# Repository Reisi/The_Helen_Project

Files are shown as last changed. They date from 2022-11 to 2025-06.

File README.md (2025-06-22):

# Helen

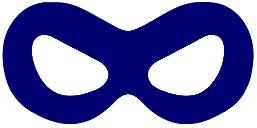
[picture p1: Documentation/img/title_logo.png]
Helen


The Helen Project is a firmware platform for bicycle lights.
It features

- up to 8 modes, each individually configurable
- the modes can be split into groups
- support for remote control connected over BLE
- mode and group configurations with The Helen App
- light-to-light connections with mode synchronization

Currently there are two devices:

- [Helen](HELEN.md), an alternative electronic circuit for the Yinding or KD2 headlight cycling lamps
- [Drake](https://github.com/Reisi/Drake), a multi-purpose PCB, which can be used to build a rear light or a dropper post actuator

## License

This project is licensed under the BSD-2-clause License - see the [license.txt](license.txt) file for details

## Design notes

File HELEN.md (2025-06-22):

# Helen

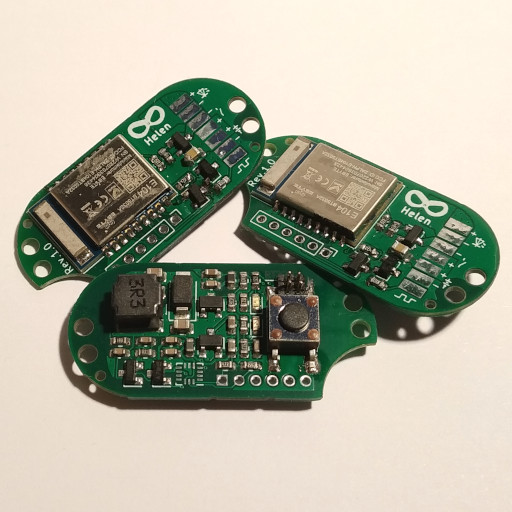
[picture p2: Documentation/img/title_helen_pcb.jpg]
Helen
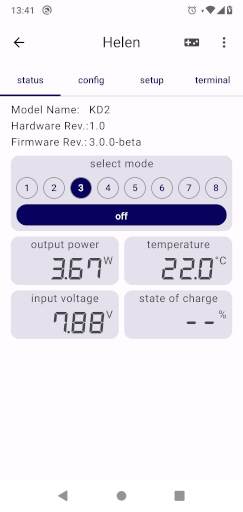
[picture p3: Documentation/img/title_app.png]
app
 

Helen is an alternative circuit board for the Yinding or KD2 headlight cycling lamps

## Main Features

- Step-Down current converter with up to 3A.
- Linear power reduction at low battery and high temperature.
- Standby current less than 100µA.
- Supports 1 (one LED), 2 (one or two LEDs) or 3 (up to three LEDs in series) cell Li-Ion battery.
- optionally: An integrated motion sensor to control the output current to reduce glare when looking down.
- optionally: A 3A PWM source.
- optionally: A multi-functional com pin, can be used for wired communication, an external button or a low power PWM source
- support for the Helena Base Driver to add two additional 3A current sources.

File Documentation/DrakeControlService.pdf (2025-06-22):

## Drake Control Service

## Base UUID: 4F770000ED7D-11E4-840E-0002A5D5C51B

## Service UUID: 0x0601

## Abstract:

This service exposes board specific control methods .

## Summary:

### TODO

## Service Dependencies:

This service is not dependent upon any other service.

## GATT Requirements

Sub-Procedure | Server Requirement
Write Characteristic Value | Mandatory
Notifications | Excluded
Indications | Mandatory
Read Characteristic Descriptors | Mandatory
Write Characteristic Descriptors | Mandatory

## Transport Dependencies

Transport | Supported
Classic | false
Low Energy | true
High Speed | false

## Error Codes

Name | Code | Description

## Service Characteristics

Overview | Properties | Security | Descriptors
Name: Drake Status Requirement: Optional | | | None
Property | Requirement | | Overview | Permissions
Perm. | Req.
Read | Mandatory
Write | Mandatory
Read | Mandatory
Write | Excluded
WriteWithoutResponse | Excluded
SignedWrite | Excluded
Notify | Mandatory
Indicate | Excluded
WriteableAuxiliaries | Excluded
Broadcast | Excluded
ExtendedProperties
Name: Drake Feature Requirement: Mandatory | | None | None

Name:
Client
Characteristic
Configuration
Requirement:
Mandatory
Property | Requirement
Read | Mandatory
Write | Excluded
WriteWithoutResponse | Excluded
SignedWrite | Excluded
Notify | Excluded
Indicate | Excluded
WriteableAuxiliaries | Excluded
Broadcast | Excluded
ExtendedProperties
Name: Drake Control Point Requirement: Mandatory | Property | Requirement | Optional | Overview | Permissions
Read | Excluded | | Name: Client Characteristic Configuration Requirement: Mandatory
Perm. | Req.
Write | Mandatory | | | Read | Mandatory
WriteWithoutResponse | Excluded | | | Write | Mandatory
SignedWrite | Excluded
Notify | Excluded
Indicate | Mandatory
WriteableAuxiliaries | Excluded
Broadcast | Excluded
ExtendedProperties

## Drake Status

## Characteristic UUID: 0x0602

## Summary:

The Drake Staus characteristic is a variable length structure containing a Flags field and, based on the contents of the Flags field, may contain one or more additional fields as shown in the table below.

## Value Fields

Names | Field Req. | Format | Additional Information
Flags | Mandatory | 8bit | Bit Field
Bit | Size | Name | Definition
0 | 1 | plunger status present
0 | False
1 | True
1 | 7 | reserved for future use
Plunger Status Information: Unit is in percent with a resolution of 0.5 Unit: org.bluetooth.unit.percentage Exponent: Binary, -1 | Optional | uint8 | 0% closed 100% fully opened

## Drake Feature

## Characteristic UUID: 0x0603

## Summary:

The Drake Feature characteristic is used to report a list of features supported by the device.

## Value Fields

Names | Field Req. | Format | Additional Information
Device Features | Mandatory | 8bit | Bit Field
Bit | Size | Name | Definition
0 | 1 | light supported
0 | False
1 | True
1 | 1 | seat-post actuator supported
0 | False
1 | True
2 | 6 | reserved for future use
Light Features | Mandatory | 8bit | Bit Field
Bit | Size | Name | Definition
0 | 1 | front-light pattern supported
0 | False
1 | True
1 | 1 | tail-light pattern supported
2 | 1 | position-light pattern supported | 0 | False
| | | 1 | True
3 | 1 | brake-light pattern supported
0 | False
1 | True
0 | False
1 | True
4 | 1 | left indicator-light pattern supported
0 | False
1 | True
5 | 1 | right indicator-light pattern supported
6 | 2 | reserved for future use
Actuator Features | Mandatory | 8bit | Bit Field
Bit | Size | Name | Definition
0 | 1 | motor configuration supported | 0 | False
| | | 1 | True
0 | False
1 | True

1 | 1 | motor sensor supported | 0 | False 1 True
2 | 1 | travel sensor supported
| | | 0 | False 1 True
4 | 4 | reserved for future use
0 | False 1 True
3 | 1 | travel indexing supported

## Drake Control Point

## Characteristic UUID: 0x0604

## Summary:

The Drake Control Point characteristic is used to request a specific function to be executed on the receiving device.

## Value Fields

Names | Field Req. | Format | Additional Information
Op codes | Mandatory | uint8 | Enumerations
Key | Value | Description
1 | request device usage | Request the devices main usage. The response to this control point is 0x20 followed by the devices usage. See Table 1: Device usage enumeration for usage definitions.
2 | set device usage | Initiate the procedure to set the devices main usage. The new usage is sent with preceding Op Code 0x02. The response to this control point is 0x20. See Table 1: Device usage enumeration for usage definitions.
3 | request battery information | Request the battery information. The response to this control point is 0x20 followed by the battery information See Table 2: Battery information for battery information definitions
4 | set battery information | Initiate the procedure to set the battery information. The new information is sent with preceding Op Code 0x04. The response to this control point is 0x20. See Table 2: Battery information for battery information definitions
5 | request soc at startup timeout | Request the state of charge at startup timeout. The response to this control point is 0x20 followed by the timeout in 1/1024s. This represents the length of one morse dot when device is used at dropper actuator and when device is used at light it represents the time in 1/1024s the indication is shown.

6 | set soc at startup timeout | Initiate the procedure to set the state of charge at startup timeout. The new timeout is sent with preceding Op Code 0x06. The response to this control point is 0x20. This represents the length of one morse dot when device is used at dropper actuator and when device is used at light it represents the time in 1/1024s the indication is shown.
7 | request light pattern | Request the current light pattern. The desired light type is sent as an uint8 with preceding Op Code 0x07. The response to this control point is 0x20 followed by the light type as uint8 and pattern as an array of uint8. See Table 3: Light type enumeration for light types and Table 4: Pattern description for pattern description.
8 | set light pattern | Initiate the procedure to change the light pattern. The desired light type (as uint8) and new pattern (as an array of uint8) is sent with preceding Op Code 0x08. The response to this control point is 0x20. See Table 3: Light type enumeration for light types and Table 4: Pattern description for pattern description.
10 | set plunger position | Initiate the procedure to set the plunger opening value. The requested opening value (in percent with a resolution of 0.5) is sent with preceding Op Code 0x09. The response to this control point is Op Code 0x20.
11 | request motor configuration | Request the current motor configuration. The response to this Op Code is 0x20 followed by the motor configuration. See Table 5: Motor configuration for configuration description.
12 | set motor configuration | Initiate the procedure to set the motor configuration. The new configuration is sent with preceding Op Code 0x0C. The response to this control point is 0x20. See Table 5: Motor configuration for configuration description.

13 | request motor sensor calibration | Request the motor sensor calibration data. The desired calibration type is sent with preceding Op Code 0x0D. The response to this control point is 0x20 followed by the calibration data. See Table 6: Motor sensor calibration data for sensor calibration data
14 | clear/start motor sensor calibration | Initiate the procedure to clear or start the desired motor sensor calibration. The desired calibration type is sent as uint8 with preceding Op Code 0x0E, followed by 0 to clear current data or 1 to start the calibration. The response to this control point is 0x20 followed by the new calibration data (in case of starting). See Table 6: Motor sensor calibration data for sensor calibration data
15 | request travel sensor data | Request the travel sensor data. The response to this control point is 0x20 followed by the sensor data data. See Table 7: Travel sensor data for sensor data
16 | clear/start motor sensor calibration | Initiate the procedure to clear or start the travel sensor calibration. To clear the sensor data send Op Code 0x10 without any data. To start the calibration send Op Code ßx10 followed with the seatpost travel in mm (as uint16). The response to this control point is 0x20 followed by the new sensor data (in case of starting). See Table 7: Travel sensor data for sensor data
17 | request indexed travel configuration | Request the indexed travel configuration. The response to this control point is 0x20 followed by the configuration. See Table 8: Indexed travel configuration
18 | set indexed travel configuration | Initiate the procedure to set the indexed travel configuration. The new configuration is sent with preceding Op Code 0x12. The response to this control point is 0x20. See Table 8: Indexed travel configuration
32 | Response Code | The response code is followed by the requested Op Code, the response value and optionally the response parameter

0-0 | Reserved for future use
15-31 | Reserved for future use
33-255 | Reserved for future use
Parameter Value | Optional | variable | Refer to the Op Code table above for additional information on the possible values for this filed
Request Op Code Information: The Request Op Code is a sub field of the Parameter Value for "Response Code" Op Code. C1: This Field is Mandatory for "Response Code" Op Code, otherwise this field is Excluded. | C1 | uint8 | Refer to the Op Code table above for additional information on the possible values for this filed
Response Value Information: The Request Op Code is a sub field of the Parameter Value for "Response Code" Op Code. C1: This Field is Mandatory for "Response Code" Op Code, otherwise this field is Excluded. | C1 | uint8 | Enumerations
Key | Value | Description
1 | Success | Response for successful operation.
2 | Op Code not supported | Response if unsupported Op Code is received.
3 | Invalid Parameter | Response if Parameter received does not meet the requirements of the service or is outside of the supported range
4 | Operation Failed | Response if the requested procedure failed
0-0 | Reserved for future use
5-255 | Reserved for future use
Response Parameter Information: The Response Parameter is a sub field of the Parameter Value for "Response Code" Op Code. C2:This Field is Optional for "Response Code" Op Code, otherwise this field is Excluded. | C2 | variable | Note: The Response Parameter Value of the response to the Control Point is a variable length field to allow a list of different values defined by the Service Specification
Key | Name | Additional Information
0 | Dropper actuator
16 | 16 LED rear light
44 | 44 LED rear light
1-15, 17-43, 45-255 | Reserved for future use

### Table 1: Device usage enumeration

Name | Format | Additional Information
type | | | cell chemistry
Key | Name
0 | LCO
1 | NMC
1-255 | Reserved for future use
design capacity Information: Unit is in Coulomb with a resolution of 1 Unit: org.bluetooth.unit.elctric_charge_coulomb Exponent: Decimal, 0 | uint16
actual capacity Information: Unit is in Coulomb with a resolution of 1 Unit: org.bluetooth.unit.elctric_charge_coulomb Exponent: Decimal, 0 | uint16 | This information is only mandatory when requesting. When setting the battery information this filed is excluded.

### Table 2: Battery information

Key | Name | Additional Information
0 | Front light
1 | Rear light
2 | Position light
3 | Brake indicator light
4 | Left indicator light
5 | Right indicator light
6-255 | Reserved for future use

### Table 3: Light type enumeration

Name | Format | Additional Information
pattern | array of uint8
| bit 7 | bit 6 | bit 5 | bit 4 | bit 3 | bit 2 | bit 1 | bit 0
pattern[0] | LED8 | LED7 | LED6 | LED5 | LED4 | LED3 | LED2 | LED1
pattern[1] | LED16 | LED15 | LED14 | LED13 | LED12 | LED11 | LED10 | LED9
pattern[n] | LED8n | LED8n-1 | LED8n-2 | LED8n-3 | LED8n-4 | LED8n-5 | LED8n-6 | LED8n-7

### Table 4: Pattern description

Name | Format | Additional Information
open timeout Information: Unit is in seconds with a resolution of 1/1024 Unit: org.bluetooth.unit.time.second Exponent: Binary, -10 | uint16 | The time the actuator motor will be activated to open. This timeout is only used if no motor sensor is available or not calibrated yet
close timeout Information: Unit is in seconds with a resolution of 1/1024 Unit: org.bluetooth.unit.time.second Exponent: Binary, -10 | uint16 | The time the actuator motor will be activated to close

### Table 5: Motor configuration

Name | Format | Additional Information

calibration type

Key | Name
0 | comp threshold | the comparator thresholds used for the sensor
1 | full open count | the number of counts until the plunger is in fully open position
2-255 | Reserved for future use
upper comp threshold Information: Unit-less with a resolution of 1 Exponent: Decimal, 0 Information: This field is mandatory for “comp threshold”, otherwise excluded | uint8 | If both, upper and lower thresholds are 0, sensor hasn’t been calibrated yet
lower comp threshold Information: Unit-less with a resolution of 1 Exponent: Decimal, 0 Information: This field is mandatory for “comp threshold”, otherwise excluded | uint8
full open count Information: Unit-less with a resolution of 1 Exponent: Decimal, 0 Information: This field is mandatory for “fully open count”, otherwise excluded | uint16

### Table 6: Motor sensor calibration data

Name | Format | Additional Information
seatpost travel Information: Unit is in millimeters with a resolution of 1 Unit: org.bluetooth.unit.length.metre Exponent: Decimal, -3 | uint16
sensor offset Information: Unit is in micrometers with a resolution of 1 Unit: org.bluetooth.unit.length.metre Exponent: Decimal, -6 | int32

### Table 7: Travel sensor data

Name | Format | Additional Information
opening blocking time Information: Unit is in seconds with a resolution of 1/1024 Unit: org.bluetooth.unit.time.second Exponent: Binary, -10 | uint16 | The time the opening position is ignored
closing timeout Information: Unit is in seconds with a resolution of 1/1024 Unit: org.bluetooth.unit.time.second Exponent: Binary, -10 | uint16 | The timeout to close when no indexed position is reached.
indexed positions Information: Unit is in millimeters with a resolution of 1 Unit: org.bluetooth.unit.length.metre Exponent: Decimal, -3 | array of int16

### Table 8: Indexed travel configuration

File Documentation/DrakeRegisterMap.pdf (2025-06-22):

## Drake I2C Register Map

Name | Address | bit 7 | bit 6 | bit 5 | bit 4 | bit 3 | bit 2 | bit 1 | bit 0
PWR | 0x00 | | | | | | | | SYS OFF
STATUS0 | 0x01 | | | | | | | TPR | MPR
STATUS1 | 0x02 | | | TOR | MOR | | | TDR | MDR
MDATA | 0x03 | MT_POS
TDATA | 0x04 | TRV_DATA
WHOAMI | 0x05 | WHO_AMI
MTCFG0 | 0x06 | DC_OPEN
MTCFG1 | 0x07 | DC_CLOSE
MTCFG2 | 0x08 | TIMEOUT_OPEN
MTCFG3 | 0x09 | TIMEOUT_CLOSE
MTCAL0 | 0x0A | | | FOS | THS | | | FOC | THC
MTCAL1 | 0x0B | | | | THR_LOW
MTCAL2 | 0x0C | | | | THR_UP
MTCAL3 | 0x0D | FULL_OPEN_L
MTCAL4 | 0x0E | FULL_OPEN_H
TRVCAL0 | 0x0F | | | | | | | | TOC
TRVCAL1 | 0x10 | TRV_POST_L
TRVCAL2 | 0x11 | TRV_POST_H
TRVCAL3 | 0x12 | TRV_OFF_L
TRVCAL4 | 0x13 | TRV_OFF_H
INDCFG0 | 0x14 | OPEN_BLOCKING
INDCFG1 | 0x15 | CLOSE_TIMEOUT
INDPOS0 | 0x16 | INDEX_POS0
INDPOS1 | 0x17 | INDEX_POS1
INDPOS2 | 0x18 | INDEX_POS2
INDPOS3 | 0x19 | INDEX_POS3

## Drake I2C Register Description

## PWR (0x00)

0 | 0 | 0 | 0 | 0 | 0 | 0 | SYS_OFF
SYS_OFF | | System off read/write default value: 0

0: system on; 1 system off
write 1 to request system off mode, device will automatically wake up on
| | bus activity

## STATUS0 (0x01)

0 | 0 | 0 | 0 | 0 | 0 | TPR | MPR
MPR | Motor position sensor present read only 0: sensor not present; 1: sensor present if sensor not present write operation to corresponding registers (MTCFG, MTCAL) have no effect
TDR | Travel sensor present read only 0: sensor not present; 1: sensor present if sensor not present write operation to corresponding registers (TRVCFG, TRVCAL) have no effect

## STATUS1 (0x02)

0 | 0 | TOR | MOR | 0 | 0 | TDR | MDR
MDR | Motor position data ready read only default value: 0 0: no new data; 1: new data available will be cleared by reading MDATA register
TDR | Travel data ready read only default value: 0 0: no new data; 1: new data available will be cleared by reading TDATA registers
MOR | Motor position data overrun read only 0: no overrun occurred; 1: previous data has been overwritten will be cleared by reading MDATA register
TOR | Travel data overrun read only 0: no overrun occurred; 1: previous data has been overwriten will be cleared by reading TDATA registers

## MDATA (0x03)

Motor position sensor data
read only
represents the motor position in q8_t (255..0 → 100..0%)

## TDATA (0x04)

Travel sensor data
read only
represents the travel in q8_t (255..0 → 100..0%)

## WHOAMI (0x05)

Who Am I
read onla
default value: 0xDE

## MTCFG0 (0x06)

Motor configuration register 0, duty cycle open read/write
represents the duty cycle used when motor is opening

## MTCFG1 (0x07)

Motor configuration register 1, duty cycle close read/write
represents the duty cycle used when motor is closing

## MTCFG2 (0x08)

Motor configuration register 2, timeout open
read/write
represents the motor timeout in 1/128s used when motor is opening

## MTCFG3 (0x09)

Motor configuration register 3, timeout close
read/write
represents the motor timeout in 1/128s used when motor is closing

## MTCAL0 (0x0A)

0 | 0 | FOS | THS | 0 | 0 | FOC | THC
THC | Threshold calibration data clear write only 0: no change; 1: threshold calibration data will be cleared
FOC | Full open calibration data clear write only 0: no change; 1: full open calibration data will be cleared
THS | Threshold calibration start write only 0: no change; 1: start threshold calibration
FOS | Full open calibration start write only 0: no change; 1: start full open calibration

## MTCAL1 (0x0B)

0 | 0 | 0 | | | THR_LOW
THR_LOW | Lower threshold calibration data
| | read only

## MTCAL2 (0x0C)

0 | 0 | 0 | | | THR_UP
THR_UP | Upper threshold calibration data
| | read only

## MTCAL3 (0x0D), MTCAL4 (0x0E)

Motor calibration register 3 and 4, full open calibration data read only

## TRVCAL0 (0x0F)

0 | 0 | 0 | 0 | 0 | 0 | 0 | TOC
T=C | Travel Offset calibration data clear
| | write only
0: no change; 1: offset calibration data will be cleared

## TRVCAL1 (0x10), TRVCAL2 (0x11)

Travel calibration register 1 and 2, seatpost travel read/write (write initiates offset calibration) represents the total travel of the seatpost in mm

## TRVCAL3 (0x12), TRVCAL4 (0x13)

Travel calibration register 3 and 4, travel sensor offset read only
represents the offset in µm (might be changed in future)

## INDCFG0 (0x14)

Indexed travel configuration register 0, opening blocking time read/write
represents the opening blocking time in 1/64s

## INDCFG1 (0x15)

Indexed travel configuration register 1, closing timeout read/write
represents the closing timeout in 1/64s

## INDPOS0 (0x16) - INDPOS3 (0x19)

Indexed travel position registers 0 to 3, indexed positions 0 - 3 read/write
represents indexed positions in q8_t

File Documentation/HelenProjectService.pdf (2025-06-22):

## Helen Project Service

## Base UUID: 4F770000ED7D-11E4-840E-0002A5D5C51B

## Service UUID: 0x0301

## Abstract:

### This service exposes measurement and control methods

## Summary:

### TODO

## Service Dependencies:

This service is not dependent upon any other service.

## GATT Requirements

Sub-Procedure | Server Requirement
Write Characteristic Value | Mandatory
Notifications | C1
Indications | Mandatory
Read Characteristic Descriptors | Mandatory
Write Characteristic Descriptors | Mandatory
C1: Mandatory if the Helen Measurement characteristic is supported, otherwise excluded for this service.

## Transport Dependencies

Transport | Supported
Classic | false
Low Energy | true
High Speed | false

## Error Codes

Name | Code | Description

## Service Characteristics

Overview | Properties | Security | Descriptors
Name: Helen Measurement Requirement: Optional | | | None
Property | Requirement | | Overview | Permissions
Perm. | Req.
Read | Mandatory
Write | Mandatory
Read | Excluded
Write | Excluded
WriteWithoutResponse | Excluded
SignedWrite | Excluded
Notify | Mandatory
Indicate | Excluded
WriteableAuxiliaries | Excluded
Broadcast | Excluded
ExtendedProperties
Name: Helen Feature Requirement: Mandatory | | None | None

Name:
Client
Characteristic
Configuration
Requirement:
Mandatory
Property | Requirement
Read | Mandatory
Write | Excluded
WriteWithoutResponse | Excluded
SignedWrite | Excluded
Notify | Excluded
Indicate | Excluded
WriteableAuxiliaries | Excluded
Broadcast | Excluded
ExtendedProperties
Name: Helen Modes Requirement: Mandatory | Property | Requirement | Optional for write property | None
| Read | Mandatory
| Write | Optional
| WriteWithoutResponse | Excluded
| SignedWrite | Excluded
| Notify | Excluded
| Indicate | Excluded
| WriteableAuxiliaries | Excluded
| Broadcast | Excluded
| ExtendedProperties

Name: Helen Control Point Requirement: Mandatory | Optional
Property | Requirement | Overview | Permissions
Read | Excluded | Name: Client Characteristic Configuration Requirement: Mandatory | Perm. | Req.
Write | Mandatory
| | | Read | Mandatory
WriteWithoutResponse | Excluded
| | | Write | Mandatory
SignedWrite | Excluded
Notify | Excluded
Indicate | Mandatory
WriteableAuxiliaries | Excluded
Broadcast | Excluded
ExtendedProperties
Name: Helen Support Requirement: Mandatory | | Optional
Property | Requirement | Overview | Permissions
Perm. | Req.
Read | Mandatory
Read | Excluded
Write | Excluded
WriteWithoutResponse | Excluded
SignedWrite | Excluded
Notify | Mandatory
Indicate | Excluded
WriteableAuxiliaries | Excluded
Broadcast | Excluded
ExtendedProperties

Name:
Client
Characteristic
Configuration
Requirement:
Mandatory

Write Mandatory

## Helen Measurement

## Characteristic UUID: 0x0302

## Summary:

The Helen Measurement characteristic is a variable length structure containing a Flags field and, based on the contents of the Flags field, may contain one or more additional fields as shown in the table below.

## Value Fields

Names | Field Req. | Format | Additional Information
tbd. | Mandatory | 8bit | set to 0 until defined
Flags | Mandatory | 8bit | Bit Field
Bit | Size | Name | Definition
0 | 1 | output power present
0 | False
1 | True
1 | 1 | temperature present
2 | 1 | input voltage present | 0 | False
| | | 1 | True
3 | 1 | SOC present
0 | False
1 | True
0 | False
1 | True
4 | 4 | reserved for future use
Mode | Mandatory | 8bit | OFF: 255; SOS: 254; ON: 0..n-1
Output Power Information: Unit is in watts with a resolution of 1/1000. Unit: org.bluetooth.unit.power.watt Exponent: Decimal, -3 | Optional | uint16
Temperature Information: Unit is in degree Cesius with a resolution of 1.. Unit: org.bluetooth.unit.thermodynamic_t emperature.degree_celcius Exponent: Decimal, 0 | Optional | int8

Input Voltage Information: Unit is in volts with a resolution of 1/1000. Unit: org.bluetooth.unit.electric_potential _difference.volt Exponent: Decimal, -3 | Optional | uint16
State of charge Information: Unit is in percent with a resolution of 0.5 Unit: org.bluetooth.unit.percentage Exponent: Binary, -1 | Optional | uint8

## Helen Feature

## Characteristic UUID: 0x0303

## Summary:

The Helen Feature characteristic is used to report a list of features supported by the device.

## Value Fields

Names | Field Req. | Format | Additional Information
Mode Count | Mandatory | 8bit | the number of available modes
Channel Count | Mandatory | 8bit | the number of available channels
Channel Size | Mandatory if Channel Count > 0, otherwise excluded | 16bit | this field is present as array, one for each channel Bit Field
Bit | Size | Name | Definition
0 | 8 | channel bitsize | the total size in bits of the Channels Configuration Field for this channel
8 | 4 | special feature bitsize | the number of bits used for special feature
12 | 4 | channel description
Key | Name | Additional Information
0 | User | user specific channel
1 | Current | current regulated channel
2 | Voltage | voltage regulated channel
3 | PWM | PWM channel
4 | Switch | on/off channel
5-15 | reserved for future use
Features | Mandatory | 16bit | Bit Field
Bit | Size | Name | Definition
0 | 1 | mode set supported
0 | False
1 | True
1 | 1 | search request supported
0 | False
1 | True
2 | 1 | factory reset supported
3 | 1 | mode override supported | 0 | False
| | | 1 | True
4 | 12 | reserved for future use
0 | False
1 | True

## Helen Modes

## Characteristic UUID: 0x0304

## Summary:

The Helen Modes characteristic is used to modify the modes of the device.

## Value Fields

Names | Field Req. | Format | Additional Information
| | | Bit Field
Bit | Size | Name | Definition
0 | 1 | ignore
0 | False
1 | True
1 | 1 | First_In_Group
Mode Configuration | Mandatory | 16bit | This field is present as array, one field for each mode
0 | False
1 | True
2 | 1 | Last_In_Group
0 | False
1 | True
3 | 1 | Is_Preferred_Mo de
0 | False
1 | True
4 | 1 | Is_Temporary_M ode
5 | 1 | Is_Off_Mode | 0 | False
| | | 1 | True
6 | 10 | reserved for future use
0 | False
1 | True

Channels Configuration | Optional | Variable | This field is present as two-dimensional array, one for
| | | each channel and mode. [channel 0][mode 0] [channel 0][mode 1] [channel 0][mode 2] … [channel 1][mode 0] [channel 1][mode 1] [channel 1][mode 2] … [channel 2][mode 0] [channel 2][mode 1] [channel 2][mode 2] | Bit Field
Bit | Size | Name
0 | channel bitsize – special feature bitsize | intensity
channel bitsize – special feature bitsize | special feature bitsize | modus

## Helen Control Point

## Characteristic UUID: 0x0305

## Summary:

The Helen Control Point characteristic is used to request a specific function to be executed on the receiving device.

## Value Fields

Names | Field Req. | Format | Additional Information
Op codes | Mandatory | uint8 | Enumerations
Key | Value | Description
1 | request mode | Request the current mode. The response to this control point is Op Code 0x20 followed by the current mode
2 | set mode | Set mode command. The response to this control point is Op Code 0x20
3 | request search | Initiate the procedure to start the search for a remote or other compatible light. The response to this control point is Op Code 0x20.
5 | factory reset | Initiate the procedure to perform a factory reset The response to this control point is Op Code 0x20. If the current connection is bonded, the device will disconnect.
8 | override mode | Temporary override the channel configuration for the current mode with the given one.
32 | Response Code | The response code is followed by the requested Op Code, the response value and optionally the response parameter
0, 4, 7, 9-31, 33-255 | Reserved for future use
mode | Mandatory for “set mode” Op code, otherwise excluded | uint8_t
channel configuration | Mandatory for “override mode” Op code, otherwise excluded | Variable | A list of channel configurations for each channel

Request Op Code | Mandatory for "Response Code" Op Code, otherwise this field is Excluded. | uint8 | Refer to the Op Code table above for additional information on the possible values for this filed
Response Value | Mandatory for "Response Code" Op Code, otherwise this field is Excluded. | uint8 | Enumerations
Key | Value | Description
1 | Success | Response for successful operation.
2 | Op Code not supported | Response if unsupported Op Code is received.
3 | Invalid Parameter | Response if Parameter received does not meet the requirements of the service or is outside of the supported range
4 | Operation Failed | Response if the requested procedure failed
0-0 | Reserved for future use
5-255 | Reserved for future use
mode | Mandatory for "Response Code" Op Code with “request mode” Request Op Code, otherwise this field is Excluded. | uint8_t

## Helen Support

## Characteristic UUID: 0x0306

## Summary:

The Helen Support characteristic is a variable length structure containing a Flags field and, based on the contents of the Flags field, may contain one or more additional fields as shown in the table below.

## Value Fields

Names | Field Req. | Format | Additional Information
Flags | Mandatory | 16bit | Bit Field
Bit | Size | Name | Definition
0 | 1 | time reference present
0 | False
1 | True
1 | 1 | brake indication timestamp present | 0 | False
| | | 1 | True
2 | 1 | left indicator timestamp present
0 | False
1 | True
3 | 1 | right indicator timestamp present
0 | False
1 | True
4 | 1 | inclination present
0 | False
1 | True
5 | 11 | reserved for future use
Time reference Information: Unit is in seconds with a resolution of 1/1024. Unit: org.bluetooth.unit.time.second Exponent: Binary, -10 | Mandatory if brake indication, left indicator or right indicator timestamp is present, otherwise optional for central, excluded for peripherals | uint16 | This represents the local timestamp at the server side. A Central shall send their reference to connected peripherals. A connected peripheral shall synchronize their local timestamp to the received timestamp. When sending a brake, left or right indicator stop timestamp, the server shall also include their timestamp so that the client is able to determine the duration of the indication.
Brake Indication Stop timestamp Information: Unit is in seconds with a resolution of 1/1024. Unit: org.bluetooth.unit.time.second Exponent: Binary, -10 | Optional | uint16 | tbd.

Left Indicator Stop Timestamp Information: Unit is in seconds with a resolution of 1/1024. Unit: org.bluetooth.unit.time.second Exponent: Binary, -10 | Optional | uint16 | tbd.
Right Indicator Stop Timestamp Information: Unit is in seconds with a resolution of 1/1024. Unit: org.bluetooth.unit.time.second Exponent: Binary, -10 | Optional | uint16 | tbd.
Inclination Information: Unit is in degree with a resolution of 1/100. Unit: org.bluetooth.unit.plane_angle.degr ee Exponent: Decimal, -2 | Optional | int16 | tbd.

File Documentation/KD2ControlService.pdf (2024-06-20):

## KD2 Control Service

## Base UUID: 4F770000ED7D-11E4-840E-0002A5D5C51B

## Service UUID: 0x0501

## Abstract:

This service exposes board specific control methods .

## Summary:

### TODO

## Service Dependencies:

This service is not dependent upon any other service.

## GATT Requirements

Sub-Procedure | Server Requirement
Write Characteristic Value | Mandatory
Notifications | Excluded
Indications | Mandatory
Read Characteristic Descriptors | Mandatory
Write Characteristic Descriptors | Mandatory

## Transport Dependencies

Transport | Supported
Classic | false
Low Energy | true
High Speed | false

## Error Codes

Name | Code | Description

## Service Characteristics

Overview | Properties | Security | Descriptors
Name: KD2 Feature Requirement: Mandatory | | | None | None
Property | Requirement
Read | Mandatory
Write | Excluded
WriteWithoutResponse | Excluded
SignedWrite | Excluded
Notify | Excluded
Indicate | Excluded
WriteableAuxiliaries | Excluded
Broadcast | Excluded
ExtendedProperties
Name: KD2 Control Point Requirement: Mandatory | | | Optional
Property | Requirement | Overview | Permissions
Read | Excluded | Name: Client Characteristic Configuration Requirement: Mandatory
Perm. | Req.
Write | Mandatory
| | | Read | Mandatory
WriteWithoutResponse | Excluded
| | | Write | Mandatory
SignedWrite | Excluded
Notify | Excluded
Indicate | Mandatory
WriteableAuxiliaries | Excluded
Broadcast | Excluded
ExtendedProperties

## KD2 Feature

## Characteristic UUID: 0x0502

## Summary:

The KD2 Feature characteristic is used to report a list of features supported by the device.

## Value Fields

Names | Field Req. | Format | Additional Information
Configuration Features | Mandatory | 8bit | Bit Field
Bit | Size | Name | Definition
0 | 1 | channel configuration supported
0 | False
1 | True
1 | 1 | com pin mode supported
0 | False
1 | True
2 | 1 | internal compensation supported
0 | False
1 | True
3 | 1 | external (Helena driver board) compensation Supported
4 | 1 | imu calibration Supported
0 | False
1 | True
0 | False
1 | True
5 | 3 | reserved for future use
Channel Features | Mandatory | 8bit | Bit Field
Bit | Size | Name | Definition
0 | 1 | adaptive channel supported
0 | False
1 | True
1 | 7 | reserved for future use

## KD2 Control Point

## Characteristic UUID: 0x0503

## Summary:

The KD2 Control Point characteristic is used to request a specific function to be executed on the receiving device.

## Value Fields

Names | Field Req. | Format | Additional Information
Op codes | Mandatory | uint8 | Enumerations
Key | Value | Description
1 | request channel configuration | Request a channel configuration. The desired channel is sent as an uint8 with preceding Op Code 0x01. The response is Op Code 0x20 followed by the channel configuration. See Table 1: channel configuration for configuration definition
2 | set channel configuration s | Initiate the procedure to configure a channel. The new channel configuration is with preceding Op Code 0x02 operand and desired channel number. The response to this control point is Op Code 0x20. See Table 1: channel configuration for configuration definition
3 | request Com pin configuration | Request the current Com pin configuration setup. The response is Op Code 0x20 followed by the current configuration. See Table 2: com pin enumeration for com pin definitions.
4 | set Com pin configuration | Initiate the procedure to change the Com pin configuration. The new configuration is sent with preceding Op Code 0x08. The response to this control point is Op Code 0x20. See Table 2: com pin enumeration for com pin definitions.

5 | request internal compensatio n | Request the internal compensation values. The response is Op Code 0x20 followed by compensation values. See Table 3: internal compensation for internal compensation value definitions.
6 | set internal compensatio n | Initiate the procedure to set the internal compensation values. The new compensation values are sent with preceding Op Code 0x0A. The response to this control point is 0x20. See Table 3: internal compensation for internal compensation value definitions.
7 | request external (Helena driver board) compensatio n | Request the compensation values of connected Helena driver board. The desired driver board is sent as an uint8 with preceding Op Code 0x07. If no board number is given, the first driver is selected. The response is Op Code 0x20 followed by compensation values. See Table 4: Helena driver board compensation for external compensation value definitions.
8 | set external (Helena driver board) compensatio n values | Initiate the procedure to set the external compensation values. The new compensation values are sent with preceding Op Code 0x08 and desired driver number, if no driver number is given, the first one is selected. The response to this control point is 0x20. See Table 4: Helena driver board compensation for external compensation value definitions
9 | request the imu calibration state | Request the imu calibration state. The response is Op Code 0x20 followed by the state (0 or 1)
10 | initiate the imu calibration | Initiate the procedure to calibrate the imu. The response is Op Code 0x20
32 | Response Code | The response code is followed by the requested Op Code, the response value and optionally the response parameter
0-0 | Reserved for future use
11-31 | Reserved for future use

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

Name | Format | Additional Information
Full Output Power Information: Unit is in watts with a resolution of 1/1000. Unit: org.bluetooth.unit.power.watt Exponent: Decimal, -3 | uint16 | valid range: 0 .. 40W
Output Limit Information: Unit is is in percentage with a resolution of 1, in relation to maximum output power. Unit: org.bluetooth.unit.percentage Exponent: Decimal, 0 | uint8 | valid range: 0..100%
Optic Type Information: Unit-less with a resolution of 1/128 Exponent: Binary, -7 | uint8 | enumeration:
Key | Name | Additional Information
0 | non-applicable | to use if channel is not equipped with an optic
1 | 15° optic
2 | 22° optic
3 | 30° optic
4-255 | Reserved for future use
Optic Offset Information: Unit is in degree with a resolution of 1/100. Unit: org.bluetooth.unit.plane_angle.degree Exponent: Decimal, -2 | int16 | valid range: -180..180°

### Table 1: channel configuration

Key | Name | Additional Information
0 | not used | com pin not used
1 | com | com pin used for communication
2 | button | com pin used as external button
3 | pwm | com pin used as active low open drain PWM signal
4-255 | Reserved for future use

### Table 2: com pin enumeration

Name | Format | Additional Information
voltage gain factor | uint16 | not used yet
voltage offset | int16 | not used yet
current gain factor Information: Unit-less with a resolution of 1/32768 Exponent: Binary, -15 | uint16
current offset | int16 | not used yet
temperature gain factor | uint16 | not used yet
temperature offset Information: Unit is in degree Celcius with a resolution of 1/128 Unit: org.bluetooth.unit.thermodynamic_t emperature.degree_celsius Exponent: Binary, -7 | int16

### Table 3: internal compensation

Name | Format | Additional Information
temperature offset Information: Unit is in degree Celcius with a resolution of 1/4 Unit: org.bluetooth.unit.thermodynamic_t emperature.degree_celsius Exponent: Binary, -2 | int16
left side current gain factor Information: Unit-less with a resolution of 1/128 Exponent: Binary, -7 | uint8
right side current gain factor Information: Unit-less with a resolution of 1/128 Exponent: Binary, -7 | uint8

### Table 4: Helena driver board compensation

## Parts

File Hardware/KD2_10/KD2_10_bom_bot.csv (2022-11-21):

Comment | Designator | Footprint | LCSC Part #
Conn_01x06 | J3
Conn_01x01 | J5 J7 J8 J1 J2 J4 J6
10 | R12 R13 | 0603 | C22859
5v6 | D5 | SOT-23-3 | C68542
2N7002 | Q2 | SOT-23-3 | C8545
4k7 | R11 | 0603 | C23162
10u/25V | C12 | 0805 | C15850
AO3400A | Q3 | SOT-23-3L | C20917
47k | R14 | 0603 | C25819
E104-BT5032A | U2 | WIRELM-SMD | C518912

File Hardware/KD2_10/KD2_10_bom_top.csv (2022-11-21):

Comment | Designator | Footprint | LCSC Part #
BMI160 | U1 | LGA-14 | C94021
SW_Push | SW1 | SMD-4_6.0x6.0x4.5P | C381064
SE8530X2-HF | U4 | SOT-23-3 | C115014
4µ7/16V | C9 C10 C2 | 0603 | C19666
100n | C4 C7 C11 C1 C8 C6 | 0603 | C14663
LED_RED | D4 | LED_0603 | C2286
LED_BLUE | D3 | LED_0603 | C72041
820 | R8 R6 | 0603 | C23253
120 | R7 | 0603 | C22787
Ferrite_Bead_Small | FB1 FB2 | 0603 | C1002
47k | R10 R5 | 0603 | C25819
1M | R9 | 0603 | C22935
4k7 | R3 R2 | 0603 | C23162
10 | R4 | 0603 | C22859
AO3400A | Q1 | SOT-23-3L | C20917
3µ-18 | L1 | IND-SMD | C83456
10u/25V | C3 C5 | 0805 | C15850
SS34 | D1 | SMA,DO-214AC | C8678
1k5 | R1 | 0603 | C22843
ZXCT1009F | U3 | SOT-23-3 | C83670
BAV99 | D2 | SOT-23-3 | C2500
dnp | J9

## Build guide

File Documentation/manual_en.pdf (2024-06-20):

# Helen

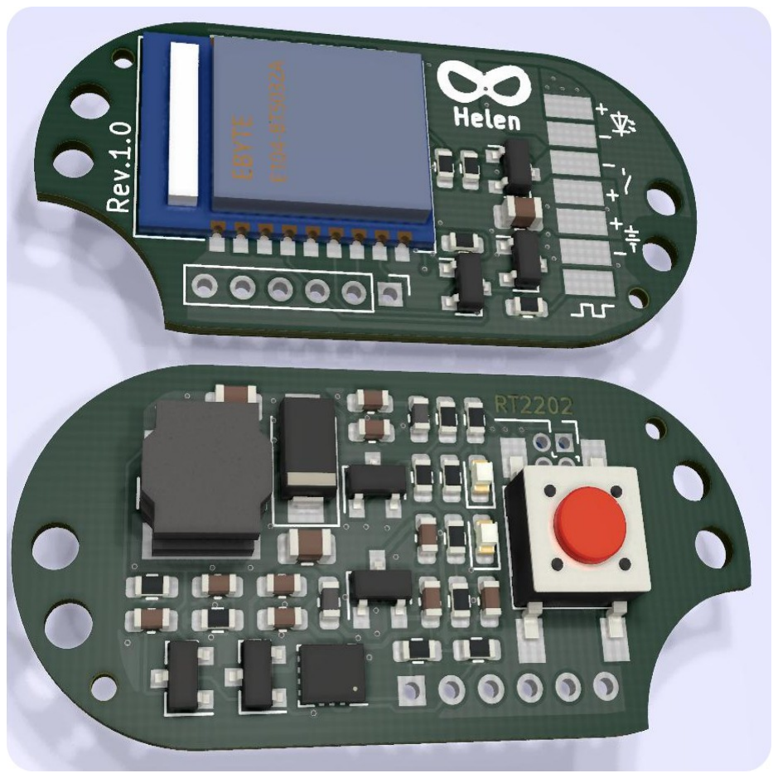
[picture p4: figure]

# User Manual

Helen User Manual

## 1 Preface

Helen is an alternative driver for the popular Yinding or KD2 Headlight Cycling Lamp with following features:
- One 3A Step-Down constant current sources, capable of driving up to three white LEDs in series.
- Bluetooth interface for wireless remote control, lamp-to-lamp connection and Smartphone based configuration.
- Integrated temperature regulation to prevent lamp from overheating.
- Smooth output power reduction when battery is low.
- Low standby current (less than 100µA).
- Works with input voltages between 3V and 4.25V (only one LED), 6V and 8.5V (up to two LEDs in series) and between 9V and 12.75V (up to three LEDs in series).
- Optionally: Integrated motion sensor to drive the LED in dependency of the head inclination, resulting in a nearly constant brightness level, no matter if you're looking down or straight forward.
- Optionally: One 3A PWM source.
- Optionally: One multi functional com pin, which can be either configured for a singe-wire communication interface, a wired external button or a low power PWM source

2/15

Helen User Manual

## Index

3/15

Helen User Manual

## 2 Connections

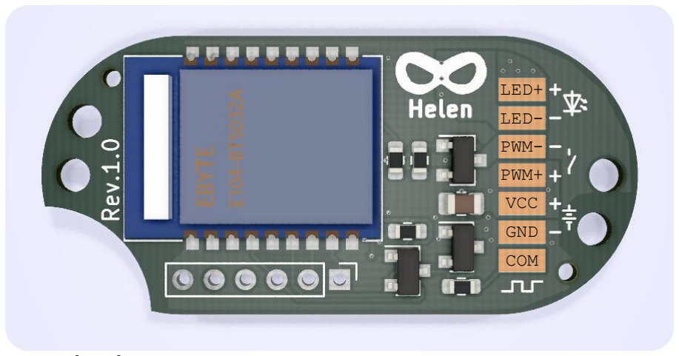
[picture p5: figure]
PWM+; PWM-; LED-; LED+; VCC GND COM

Pad | Function | additional information
LED+ | connection for LED anode | the sum of forward voltages of in series connected LEDs must be lower than the
supply voltage LED- | connection for LED catode
PWM- | return path for PWM load | this is an active low PWM channel, the +pad is connected to VCC, the -pad is switched to GND with a MOSFET capable of driving 3A (there is no protection, make sure the connected load does not draw more current)
PWM+ | source for PWM load
VCC | positive power supply | max. operational voltage: 13.5V
no reverse polarity protection! GND | negative power supply
COM | multi functional pin | open drain interface, max. voltage VCC, max. sink current 5mA

4/15

Image 1: board connections

Helen User Manual

## 3 Usage

## 3.1 Modes and Groups

Helen has 8 individual configurable modes, which can be organized in different groups.

### 3.1.1 Preferred Mode

One of the 8 available modes can be selected as the preferred mode. If the preferred mode is not selected, the lamp will shut off whenever the preferred mode is selected. If one mode is selected as the preferred mode the lamp will shut off, if it already is in the preferred mode. Otherwise it will jump to the preferred mode.

### 3.1.2 Temporary Mode

One of the 8 available modes can be selected as a temporary mode. If a mode is selected as temporary mode, it is possible to jump directly into this mode. When leaving the mode, Helen jumps back to the previously used mode.

### 3.1.3 Off Mode

One of the 8 available modes can be selected as the off mode. If a mode is selected as off mode, this mode will be used when the lamp is shut off. When the lamp enters stand-by mode (after three minutes without movement) it will completely shut off.

5/15

Helen User Manual

## 3.2 Remote Connection

Helen can manage up to 4 connections, 3 as a central (e.g. a remote control or another lamp) and 1 as peripheral (e.g. a smart phone or another lamp).
Although it is possible to pair with several remote controls, it is not possible to connect to more than one remote control simultaneously. If two lamps are connected to each other, the lamp with the peripheral connection will break its connection with a remote control and won’t reconnect as long as it is connected with the other lamp.

### 3.2.1 Central connection

To initiate a connection as central (e.g. if you want to connect to a remote control or initiate a central connection with another lamp), you have to
- shut of Helen,
- make sure, that all other unwanted compatible devices are shut of or out of range,
- press Helen’s button for at least 2 sec.
Helen will indicate the search process with a fast blinking blue status LED. As soon as a connection is established the blue status LED will be constantly on. If no device is found within 30 sec. the lamp will stop searching and starts a 30 sec. window where it is open for peripheral connections (see next chapter).

6/15

Helen User Manual

This procedure is only necessary for the initial connection. The lamp will store all necessary information and automatically reconnect if the device is available.

### 3.2.2 Peripheral connection

To initiate a connection as peripheral (e.g. if you want to connect to a smartphone or initiate a peripheral connection with another lamp), you have to
- shut of Helen,
- make sure, that all other unwanted compatible devices are shut of or out of range,
- press Helen’s button for at least 2 sec until the blue led blinks fast,
- wait 30 sec until the blue led stops fast blinking.
Now you can start the connection procedure on the central device. This procedure is only necessary for the initial connection. The lamp will store all necessary information and you can establish future connection as soon as Helen is powered on.

## 3.3 Button Control

There are 4 button control commands:
- next mode:
This command jumps to the next mode.
If the ignore flag for this mode is selected, it will be skipped.

7/15

Helen User Manual

If the last mode within a group is reached, it will roll over to the first mode.
If the light is currently off it jumps to the first mode.
- next group:
This command jumps to the next group.
If the group only contains ignored modes, it will be skipped. If the current group is the last group, this command will jump to the first group.
If the light is currently off, it jumps to the first mode in the second group.
- preferred mode:
If the preferred mode is not set, the light will shut off.
If the preferred mode is set, the light will jump directly to the preferred mode.
If the light is already in the preferred mode, it will shut off.
- temporary mode:
If the temporary mode is set, the light will jump into the temporary mode and jumps back to the previous mode.

### 3.3.1 Integrated button

- short click:
next mode command
- long click:
next group command

8/15

Helen User Manual

- press and hold > 2 sec., light is off:
initiate connection procedure
hold button again for 2 sec. to delete all bluetooth bonding data
- press and hold > 10 sec., light is off:
initiate a factory reset
- press and hold > 2 sec., light is on:
preferred mode command

### 3.3.2 External button (if available)

- short click:
next mode command
- long click:
next group command
- press and hold > 2 sec.:
preferred mode command

### 3.3.3 Xiaomi Yi remote control

- main button, short click:
next mode command
- main button, press and hold > 0.5 sec.:

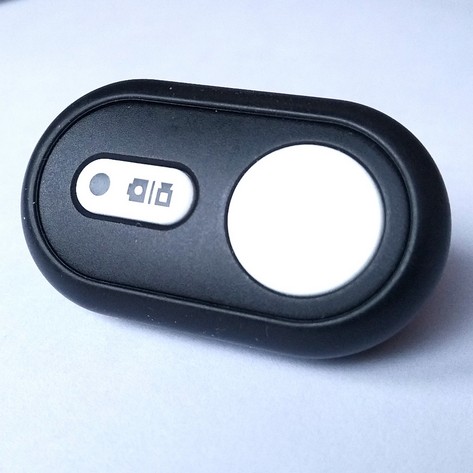
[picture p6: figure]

enter temporary mode as long as button is pressed
- secondary button, short click:
next group command

9/15

Image 2: Xiaomi Yi RC

Helen User Manual

- secondary button, press and hold > 0.5 sec.: preferred mode command

### 3.3.4 Pearl/Auvisio remote control

- next track button, short click:
next mode command
- previous track button, short click:
previous mode command
- volume up button, short click: next group command
- volume down button, short click: previous group command
- play/pause button, short click:
preferred mode command

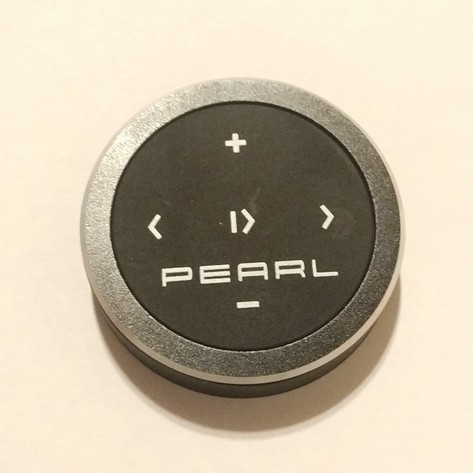
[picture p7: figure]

## 3.4 Remote Synchronization

If Helen is connected to another lamp, both lamps will synchronize their current mode. This means if one light receives a button command, it will change its mode according to the description in the previous chapter and then relay this new mode (the number, not the configuration!) to the other lamp.
This lamp will then also jump into this mode, nevertheless if this mode is used or not. With this behavior it is possible to generate configurations where one lamp is on and the other not.

10/15

Image 3: Pearl/Auvisio
remote

Helen User Manual

## 3.5 Status LED

Helen is equipped with a red and blue status LED, which is visible through the transparent button cap.
The blue LED gives information about the wireless connection. If is on, Helen is connected to a remote or another lamp. A fast blinking indicates, that Helen is searching for any compatible device. A slow blinking blue LED indicates, that Helen is searching for a already known device.
The red on turns on whenever the output is limited due to high temperature or dropping input voltage.
When Helen enters standby mode, the Status LED is shut off for minimum current consumption (but an established connection or the scanning for a known device will not be stopped).

11/15

Helen User Manual

## 4 Configuration

## 4.1 Connecting with the App

To connect to your lamp open the app and
press the SEARCH button.
The App will then search and connect to all

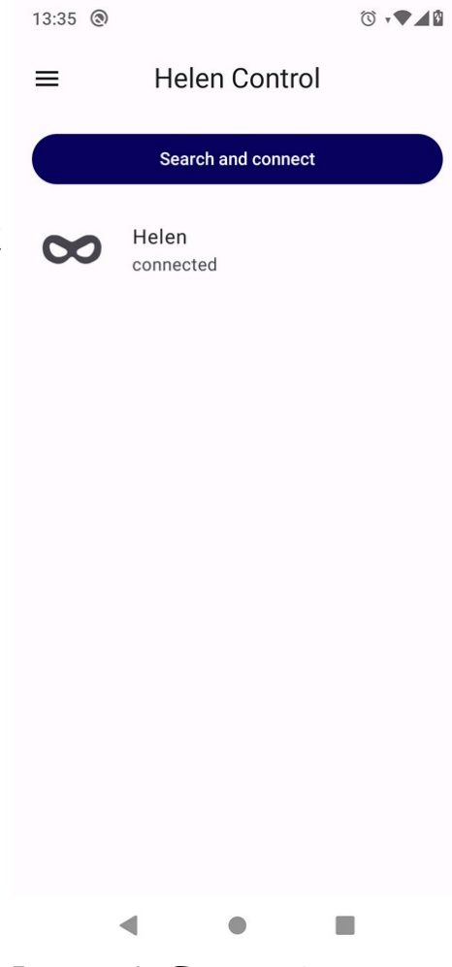
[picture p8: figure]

compatible lamps in range. Tap on the the light you want to configure.
If it is the first connection you have to follow the procedure in 3.2.2. In this case your phone will also ask you to pair with the light, which you have to confirm.

12/15

Image 4: Connecting

Helen User Manual

## 4.2 Light status

The STATUS page gives you information about the current state of the lamp.
If you tap at the control icon in the top bar you can also select any of the light modes or shut it off.

13/15

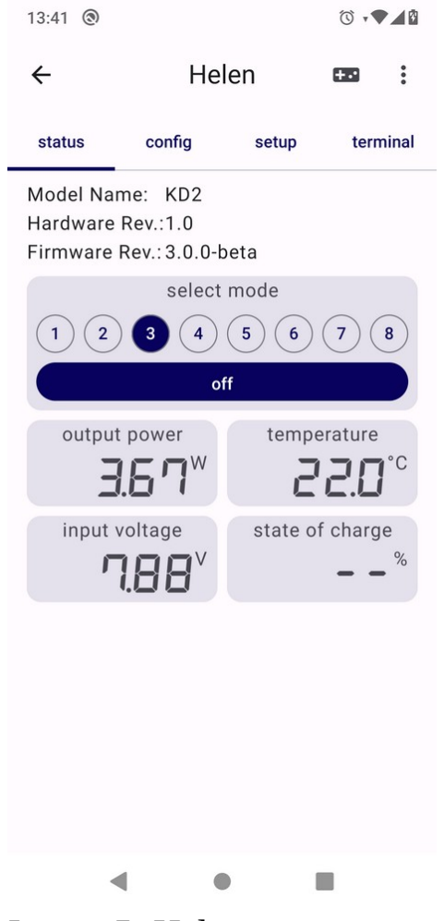
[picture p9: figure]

Image 5: Helen status

Helen User Manual

## 4.3 Configuration

On the CONFIG page
you see an overview of
your modes and the

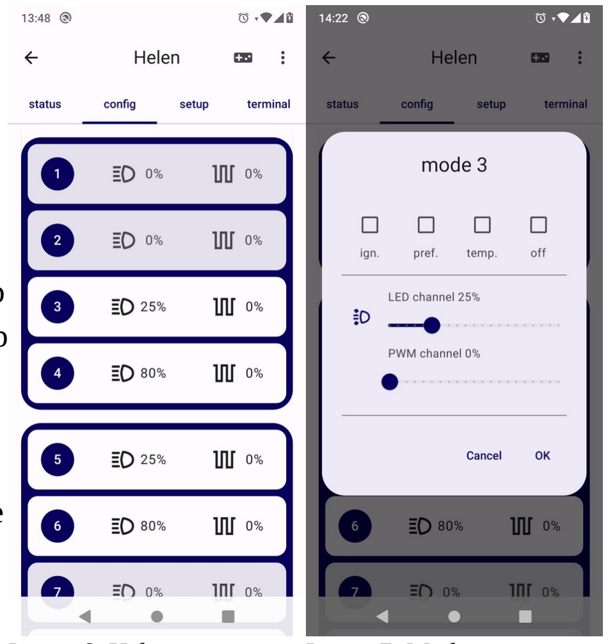
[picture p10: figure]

group arrangements. To
change the group
arrangement simply
drag and drop the group
dividers. To add a group
you can drag and drop
from the top or bottom.
To change a mode
configuration tap on the
mode. There you can
select if the mode
should be ignored, used
as preferred, temporary
or off mode and you can also select the intensity of the light and the PWM channel, and if the motion sensor should be used for to adjust the light depending on your head inclination.

14/15

Image 7: Mode
configuration

Image 6: Helen
configuration

Helen User Manual

## 4.4 Setup

On the setup page you can select how you want to use the communication pin.

15/15

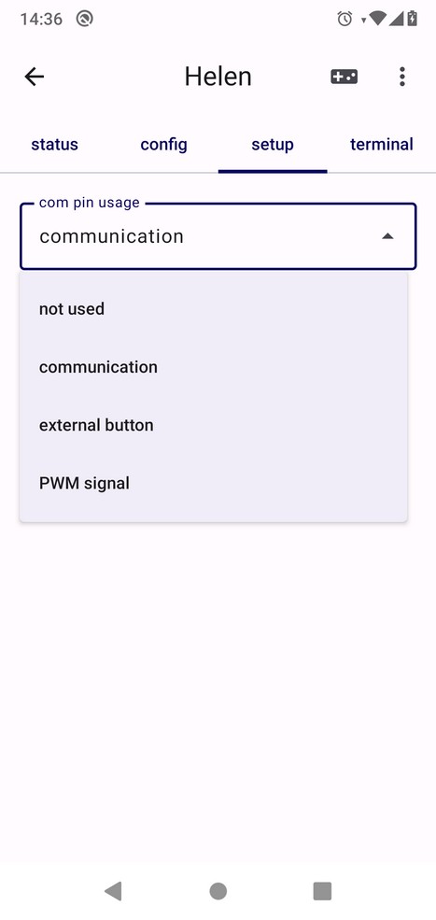
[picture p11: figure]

Image 8: Setup

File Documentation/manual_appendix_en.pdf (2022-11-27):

# Helen


# User Manual Appendix

Helen User Manual

## Index

2/4

Helen User Manual

## Appendix A Firmware Update

Currently the Light Control App does not support firmware updates yet, but the firmware can be updated with nrf connect from Nordic Semiconductors.
First download the new firmware archive (KD2_10.zip) from the Github repository in the folder Firmware/Helen/bin_debug.

Now open the App and start scanning. Connect to Helen and start the update by tapping on the small DFU icon in the top. Then select the previously downloaded firmware archive.

3/4

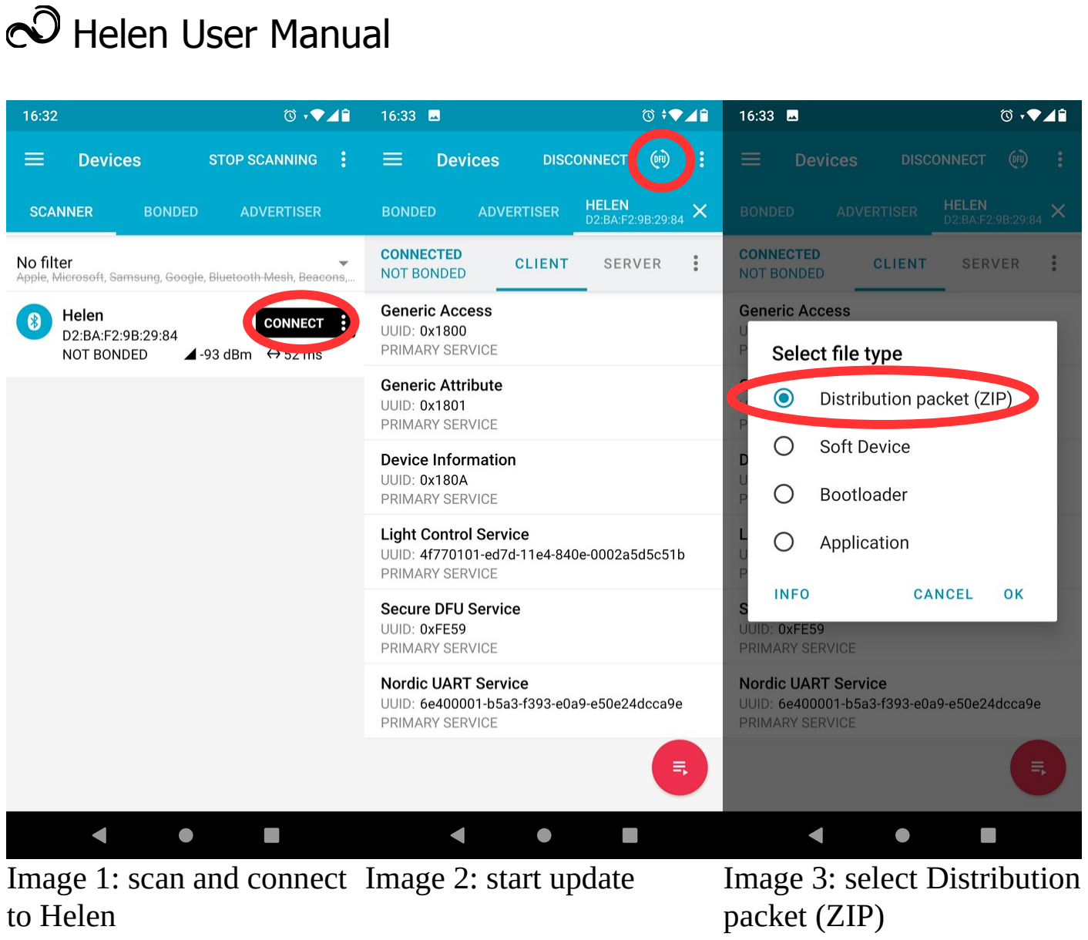
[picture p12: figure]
Helen User Manual; Image 1: scan and connect to Helen; packet (ZIP)

4/4

Image 2: start update Image 3: select Distribution

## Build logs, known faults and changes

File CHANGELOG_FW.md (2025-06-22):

# Changelog
All notable changes to the Helen firmware will be documented in this file.

The format is based on [Keep a Changelog](https://keepachangelog.com/en/1.0.0/)

## [3.2.0-beta] - 2025-06-17

### Changed
- battery info type, added LCO as 0, moved NMC to 1

### Known Issues
- unstable regulator at low currents -> visible flickering
- voltage limiter has delay
- temperature limiter overshoots

## [3.2.0-beta] - 2025-06-17
### Added
- Drake

### Known Issues
- unstable regulator at low currents -> visible flickering
- voltage limiter has delay
- temperature limiter overshoots

## [3.1.1] - 2024-06-20
### Fixed
- some minor bugs

### Known Issues
- unstable regulator at low currents -> visible flickering
- voltage limiter has delay
- temperature limiter overshoots

## [3.1.0] - 2024-03-12
### Added
- override mode (immediately see changes while configure modes in the app)

### Known Issues
- unstable regulator at low currents -> visible flickering
- voltage limiter has delay
- temperature limiter overshoots

## [3.0.0] - 2024-02-24
### Added
- dedicated service for helen project and kd2 hardware configuration
- support for changing device name
- added off mode

### Changed
- advertising and scanning reworked, whitelist is only used for scanning, advertising is handled manually

### Deprecated
- the helena configuration service will be first reduced to remote control functions and later completely removed

### Fixed
- noisy temperature measurement in idle mode
- missing report handler for factory reset
- fixed rounding error for channel angle offset
- unnecessary power field in measurement data while light is off

### Known Issues
- unstable regulator at low currents -> visible flickering
- voltage limiter has delay
- temperature limiter overshoots

## [v2-alpha] - 2022-11-21
### Added

### Changed

### Removed

### Fixed

### Known Issues
- unstable regulator at low currents -> visible flickering
- voltage limiter has delay
- temperature limiter overshoots

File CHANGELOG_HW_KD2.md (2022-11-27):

# Changelog
All notable changes to the KD2 board hardware will be documented in this file.

The format is based on [Keep a Changelog](https://keepachangelog.com/en/1.0.0/)

## [1.1] - 2022-11 - Unreleased
### Added
- green status led

### Changed
- pin rearrangement, COM pin is now on analog pin

### Removed
- INT2 pin of BMI160 not needed

### Fixed
- SD0 pin of BMI160 connected to GND

### Known Issues

## [1.0] - 2022-02
### Added

### Changed

### Removed

### Fixed

### Known Issues
- SD0 pin of BMI160 floating, needs to be connected to GND
- protection diode (D5) on COM pin should be replaced with higher voltage type
  to use pin as an open drain PWM signal output
  -> fixed, all board are/will be assembled with 18V zener
- current measurement resistor (R6) needs to be replaced with 680 Ohm, 820 Ohm
  is too close to adc measurement limits
  -> fixed, all boards are/will be reassembled with 680 Ohm resistor
- onboard antenna not working when case closed and no debugging cable connected
  -> remove onboard antenna and add external

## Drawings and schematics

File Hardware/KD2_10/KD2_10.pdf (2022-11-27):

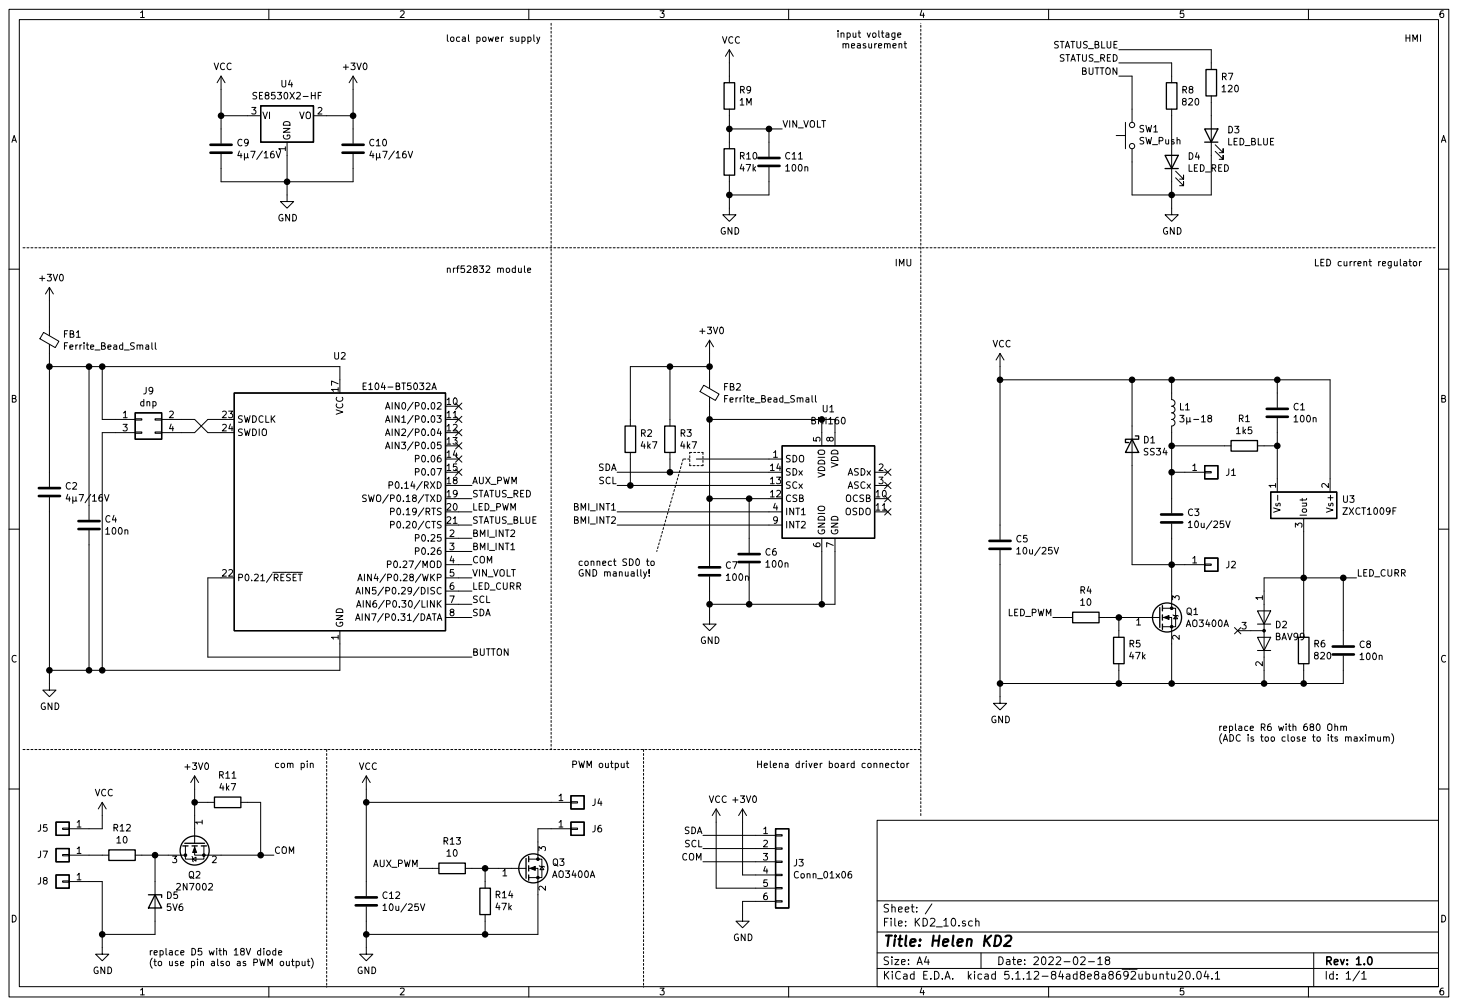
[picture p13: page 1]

1 AIN0/P0.02 10 AIN1/P0.03 11 AIN2/P0.04 12 AIN3/P0.05 13 P0.06 14 P0.07 15 VCC 17 P0.14/RXD 18 SWO/P0.18/TXD 19 P0.25 2 P0.19/RTS 20 P0.20/CTS 21 P0.21/RESET 22 SWDCLK 23 SWDIO 24 P0.26 3 P0.27/MOD 4 AIN4/P0.28/WKP 5 AIN5/P0.29/DISC 6 AIN6/P0.30/LINK 7 AIN7/P0.31/DATA 8 U2 E104-BT5032A C1 R1 100n

connect SD0 to GND manually!

replace R6 with 680 Ohm
(ADC is too close to its maximum)

replace D5 with 18V diode
(to use pin also as PWM output)

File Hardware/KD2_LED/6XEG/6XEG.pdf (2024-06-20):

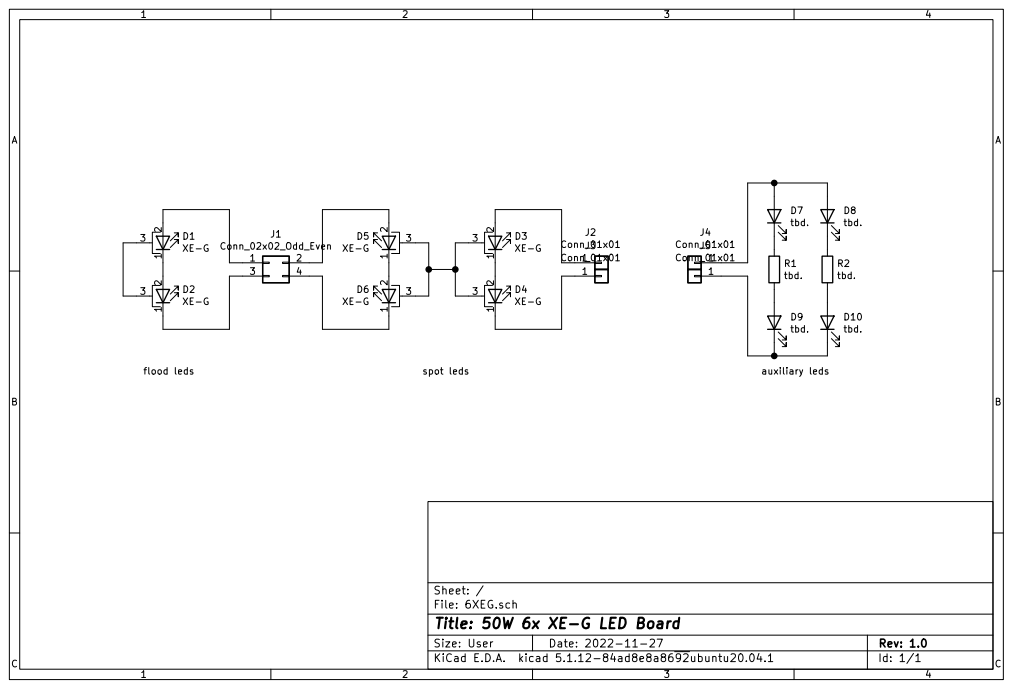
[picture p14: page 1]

Id: 1/1 Title: 50W 6x XE-G LED Board

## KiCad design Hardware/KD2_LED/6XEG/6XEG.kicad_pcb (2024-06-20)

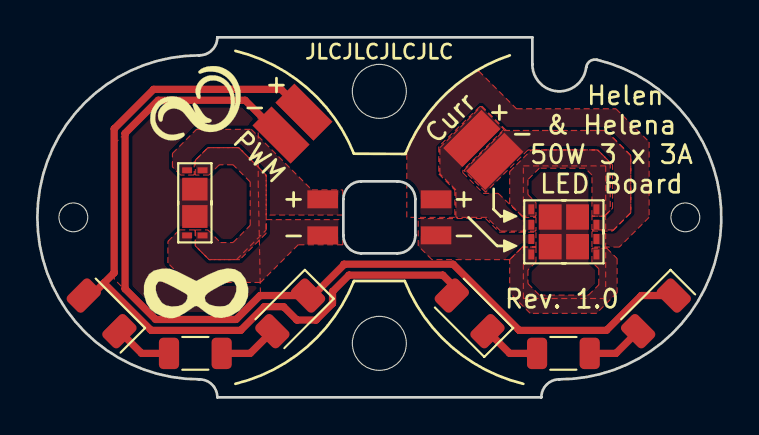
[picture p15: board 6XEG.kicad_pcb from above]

Board: 2 copper layers, 38.0 x 20.0 mm, 17 parts (0 on the bottom side), 17 nets.

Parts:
D1, D2, D3, D4, D5, D6: LED_PAD; LED_Cree-XE-G
D7, D8, D9, D10: LED; LED_1206_3216Metric
J1: Conn_02x02_Odd_Even; PinHeader_2x02_P2.00mm_Vertical_SMD
J2, J3, J4, J5: Conn_01x01; 1,5x3mm_SMD
R1, R2: R; R_1206_3216Metric

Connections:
unnamed: D1.1, D2.2
unnamed: D1.2, J1.1
unnamed: D1.3, D2.3
unnamed: D2.1, J1.3
unnamed: D3.1, D4.2
unnamed: D3.2, J2.1
unnamed: D3.3, D4.3, D5.3, D6.3
unnamed: D4.1, J3.1
unnamed: D5.1, D6.2
unnamed: D5.2, J1.2
unnamed: D6.1, J1.4
unnamed: D7.1, R1.1
unnamed: D7.2, D8.2, J4.1
unnamed: D8.1, R2.1
unnamed: D9.2, R1.2
unnamed: D9.1, D10.1, J5.1
unnamed: D10.2, R2.2

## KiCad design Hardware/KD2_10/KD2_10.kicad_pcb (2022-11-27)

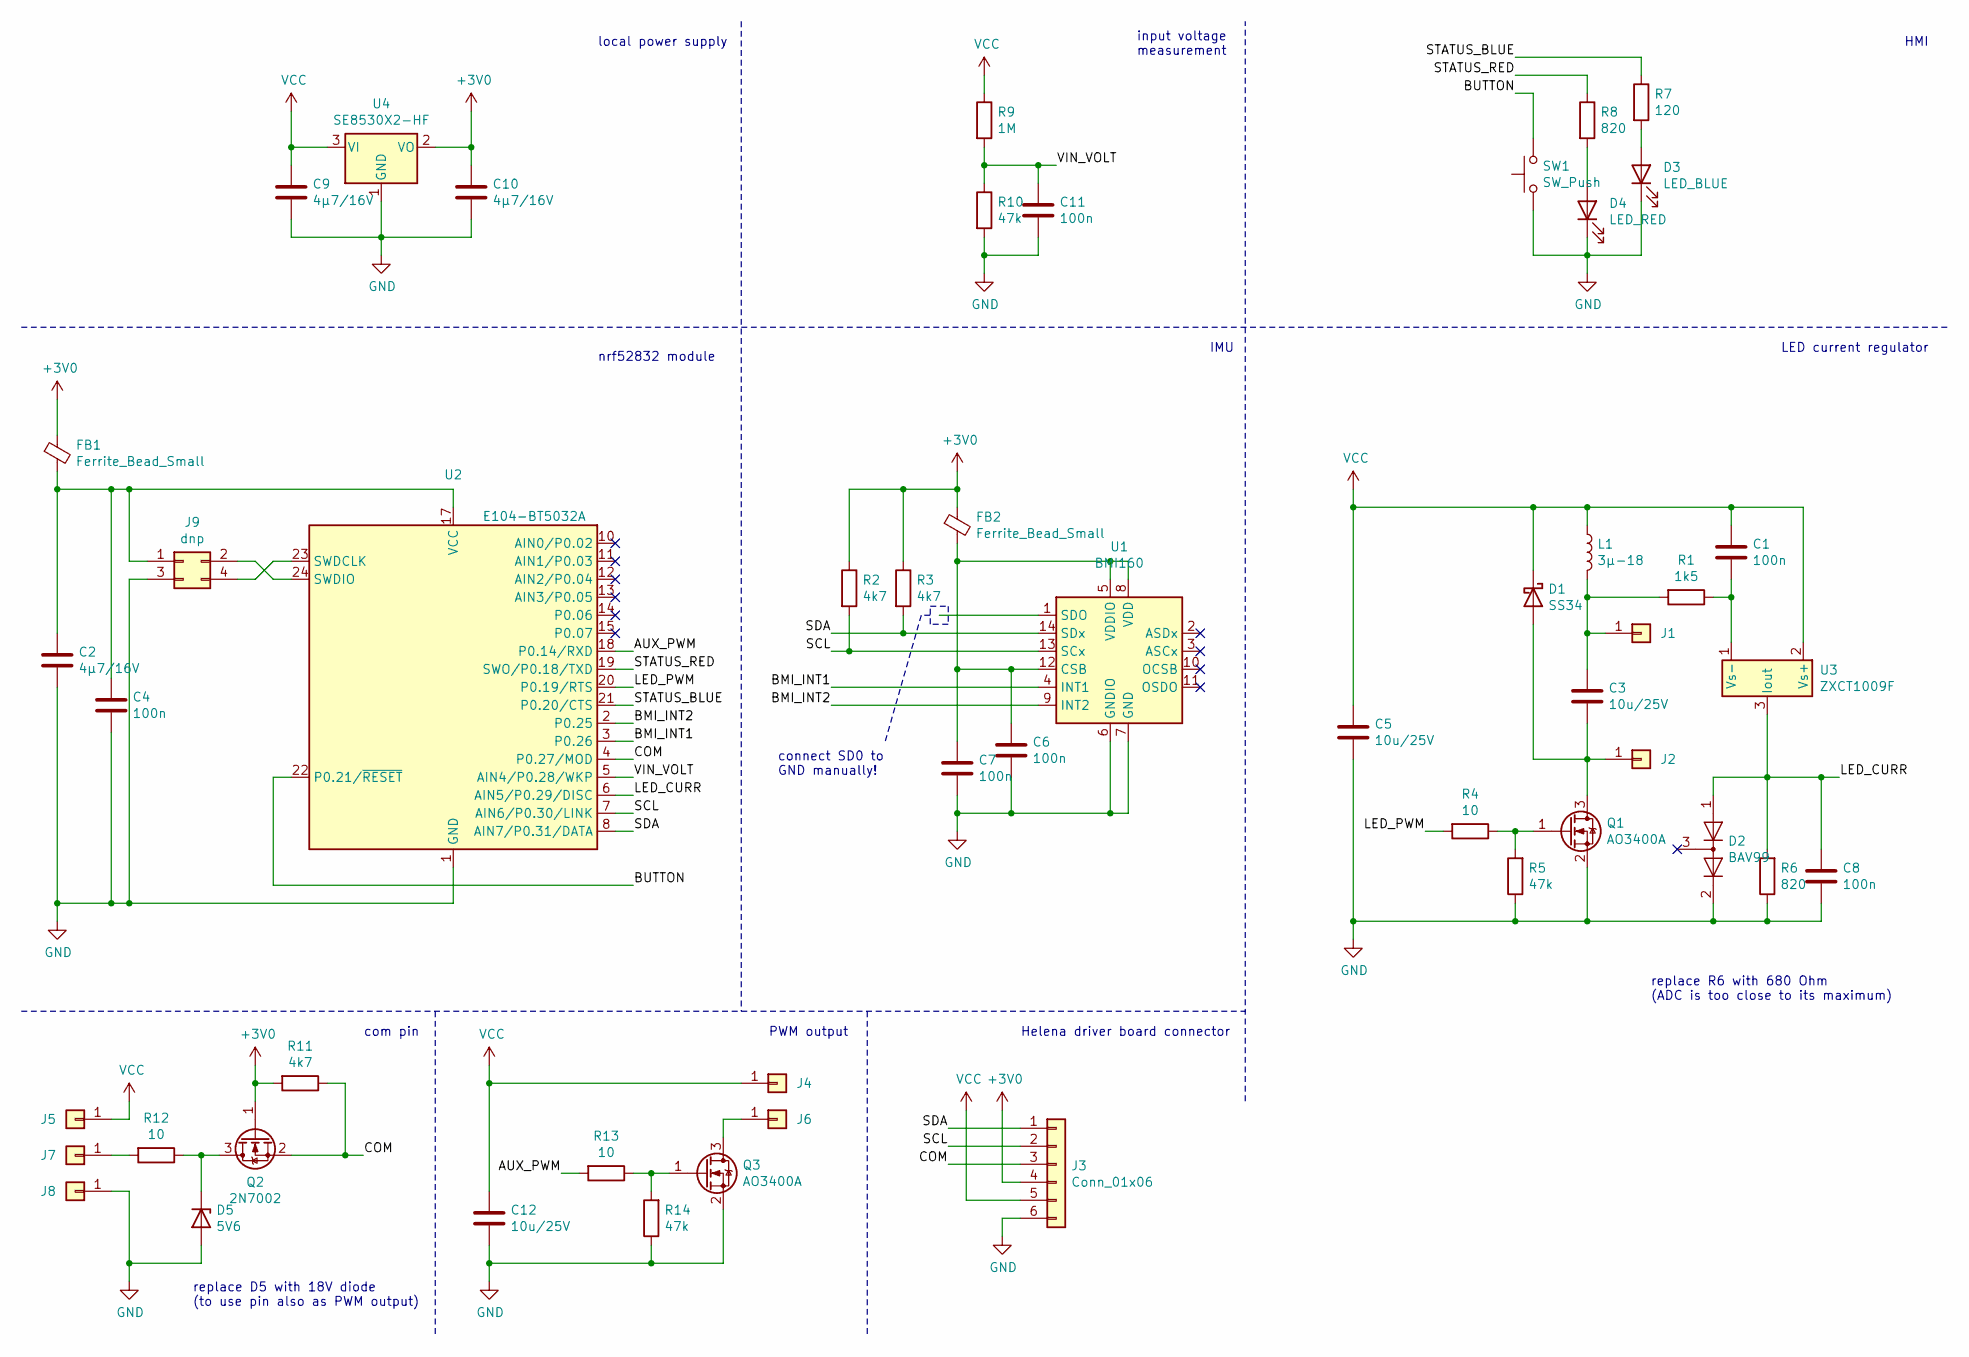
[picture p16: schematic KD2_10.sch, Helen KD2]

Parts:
C1, C4, C6, C7, C8, C11: 100n; C_0603_1608Metric; JLC 0603
C2, C9, C10: 4µ7/16V; C_0603_1608Metric; JLC 0603
C3, C5, C12: 10u/25V; C_0805_2012Metric; JLC 0805
D1: SS34; D_SMA; JLC SMA,DO-214AC
D2: BAV99; SOT-23; JLC SOT-23-3
D3: LED_BLUE; LED_0603_1608Metric; JLC LED_0603
D4: LED_RED; LED_0603_1608Metric; JLC LED_0603
D5: 5V6; D_SOT-23_ANK; JLC SOT-23-3
FB1, FB2: Ferrite_Bead_Small; L_0603_1608Metric; JLC 0603
J1, J2, J4, J5, J6, J7, J8: Conn_01x01; 1,5x3mm_SMD
J3: Conn_01x06; PinHeader_1x06_P2.00mm_Vertical
J9: dnp; PinHeader_2x02_P1.27mm_Vertical
L1: 3µ-18; Choke_SMD_Fastron_242418_FPS; JLC IND-SMD
Q1, Q3: AO3400A; SOT-23_AO3400A; JLC SOT-23-3L
Q2: 2N7002; SOT-23; JLC SOT-23-3
R1: 1k5; R_0603_1608Metric; JLC 0603
R2, R3, R11: 4k7; R_0603_1608Metric; JLC 0603
R4, R12, R13: 10; R_0603_1608Metric; JLC 0603
R5, R10, R14: 47k; R_0603_1608Metric; JLC 0603
R6, R8: 820; R_0603_1608Metric; JLC 0603
R7: 120; R_0603_1608Metric; JLC 0603
R9: 1M; R_0603_1608Metric; JLC 0603
SW1: SW_Push; JTP-1138EM; JLC SMD-4_6.0x6.0x4.5P
U1: BMI160; Bosch_LGA-14_3x2.5mm_P0.5mm; JLC LGA-14
U2: E104-BT5032A; JLC WIRELM-SMD
U3: ZXCT1009F; SOT-23; JLC SOT-23-3
U4: SE8530X2-HF; SOT-23_MCP1703; JLC SOT-23-3

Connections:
+3V0: C10.1, FB1.1, FB2.1, J3.4, Q2.1 (G), R2.1, R3.1, R11.2, U4.2 (VO)
/AUX_PWM: R13.2, U2.18 (P0.14/RXD)
/BMI_INT1: U1.4 (INT1), U2.3 (P0.26)
/BMI_INT2: U1.9 (INT2), U2.2 (P0.25)
/BUTTON: SW1.2, U2.22 (P0.21/~RESET)
/COM: J3.3, Q2.2 (S), R11.1, U2.4 (P0.27/MOD)
/LED_CURR: C8.1, D2.1 (K), R6.2, U2.6 (AIN5/P0.29/DISC), U3.3 (Iout)
/LED_PWM: R4.2, U2.20 (P0.19/RTS)
/SCL: J3.2, R2.2, U1.13 (SCx), U2.7 (AIN6/P0.30/LINK)
/SDA: J3.1, R3.2, U1.14 (SDx), U2.8 (AIN7/P0.31/DATA)
/STATUS_BLUE: R7.1, U2.21 (P0.20/CTS)
/STATUS_RED: R8.1, U2.19 (SWO/P0.18/TXD)
/VIN_VOLT: C11.1, R9.2, R10.1, U2.5 (AIN4/P0.28/WKP)
GND: C2.2, C4.2, C5.2, C6.2, C7.2, C8.2, C9.2, C10.2, C11.2, C12.2, D2.2 (A), D3.1 (K), D4.1 (K), D5.2 (A), J3.6, J8.1, J9.3, Q1.2 (S), Q3.2 (S), R5.1, R6.1, R10.2, R14.1, SW1.1, U1.6 (GNDIO), U1.7 (GND), U2.1 (GND), U2.9 (GND), U2.16 (GND), U4.1 (GND)
unnamed: C1.2, R1.1, U3.1 (Vs-)
unnamed: C2.1, C4.1, FB1.2, J9.1, U2.17 (VCC)
unnamed: C3.1, J1.1, L1.2, R1.2
unnamed: C3.2, D1.2 (A), J2.1, Q1.3 (D)
unnamed: C6.1, C7.1, FB2.2, U1.5 (VDDIO), U1.8 (VDD), U1.12 (CSB)
unnamed: D3.2 (A), R7.2
unnamed: D4.2 (A), R8.2
unnamed: D5.1 (K), Q2.3 (D), R12.1
unnamed: J6.1, Q3.3 (D)
unnamed: J7.1, R12.2
unnamed: J9.2, U2.24 (SWDIO)
unnamed: J9.4, U2.23 (SWDCLK)
unnamed: Q1.1 (G), R4.1, R5.2
unnamed: Q3.1 (G), R13.1, R14.2
VCC: C1.1, C5.1, C9.1, C12.1, D1.1 (K), J3.5, J4.1, J5.1, L1.1, R9.1, U3.2 (Vs+), U4.3 (VI)

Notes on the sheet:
com pin
PWM output
Helena driver board connector
nrf52832 module
IMU
local power supply
input voltage measurement
LED current regulator
HMI
connect SD0 to GND manually!
replace D5 with 18V diode (to use pin also as PWM output)
replace R6 with 680 Ohm (ADC is too close to its maximum)

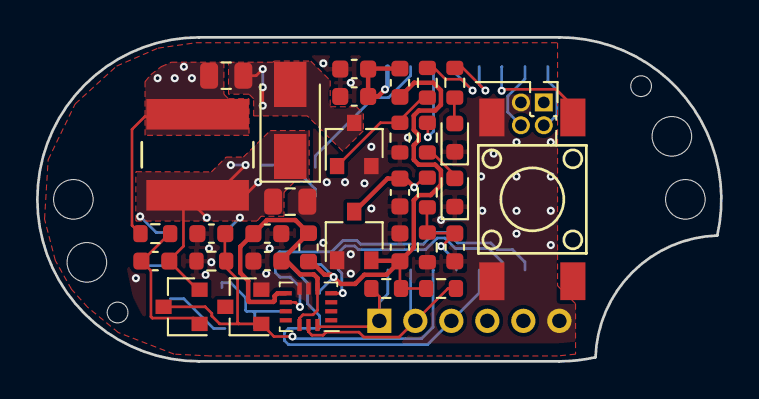
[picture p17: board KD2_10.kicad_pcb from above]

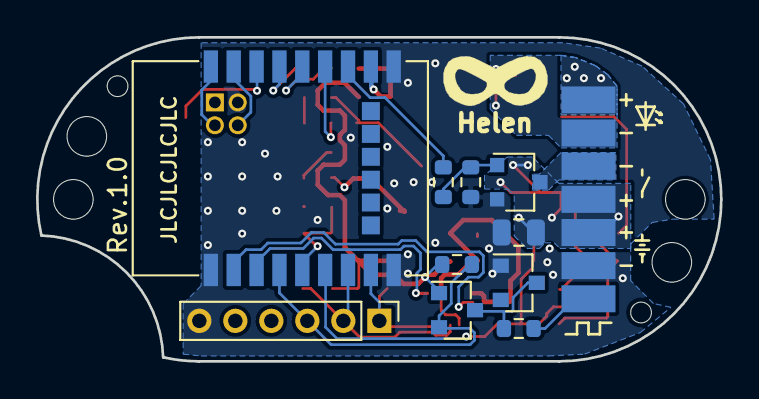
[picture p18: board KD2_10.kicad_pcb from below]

Board: 4 copper layers, 38.0 x 18.0 mm, 51 parts (17 on the bottom side), 29 nets.

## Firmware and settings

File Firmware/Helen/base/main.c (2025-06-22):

/**
  ******************************************************************************
  * @file    main.c
  * @author  Thomas Reisnecker
  * @brief   main module
  ******************************************************************************
  */

/* Includes ------------------------------------------------------------------*/
#include <stdbool.h>
#include <stdint.h>
#include <string.h>

#include "nordic_common.h"
#include "nrf.h"
#include "app_error.h"
#include "app_timer.h"
#include "nrf_sdh.h"
#include "nrf_sdh_soc.h"
#include "fds.h"
#include "nrf_pwr_mgmt.h"
//#include "nrf_drv_clock.h"
#include "nrf_power.h"
#include "nrf_bootloader_info.h"

#include "main.h"
#include "debug.h"
#include "btle.h"
#include "link_management.h"
#include "board.h"
#include "hmi.h"
#include "mode_management.h"
#include "channel_types.h"
#include "watchdog.h"
#include "com_message_handling.h"

#include "ble_types.h"

/* logger configuration ----------------------------------------------_-------*/
#define BASE_CONFIG_LOG_ENABLED 1 /// TODO: just temporary until project specific sdk_config
#define BASE_CONFIG_LOG_LEVEL   3

#define NRF_LOG_MODULE_NAME base
#if BASE_CONFIG_LOG_ENABLED
#define NRF_LOG_LEVEL BASE_CONFIG_LOG_LEVEL
#else //BASE_CONFIG_LOG_ENABLED
#define NRF_LOG_LEVEL 0
#endif //BASE_CONFIG_LOG_ENABLED
#include "nrf_log.h"
NRF_LOG_MODULE_REGISTER();

/* Private defines -----------------------------------------------------------*/
#define IDLE_TIMEOUT APP_TIMER_TICKS(180000)
#define IDLE_PERIOD  APP_TIMER_TICKS(10000)

/* Private typedef -----------------------------------------------------------*/
typedef enum
{
    MAINSTATE_OFF,      // device enters system off mode
    MAINSTATE_STANDBY,
    MAINSTATE_IDLE
} mState_t;

typedef enum
{
    FLOPSCR_NONE,   // no source
    FLOPSCR_HMI,    // flash operation request from hmi module
//    FLOPSCR_LCS,    // flash operation request from light control service
} pendingFlashOpSource_t;

typedef struct
{
    volatile uint8_t pendingResponses;           // the number of responses to be expected
    pendingFlashOpSource_t source;
    uint32_t firstErrorCode;
    union
    {
        struct
        {
            ble_lcs_ctrlpt_evt_type_t event; // the event from light control service (0 if not the source)
            uint16_t connHandle;
            ble_lcs_ctrlpt_t * pLcsCtrlpt;
        } lcs;
        ds_reportHandler_t hmiResponse;
    };                           // the source for the flash operation, only one is allowed at a timer
} pendingFlashOp_t;

/* Private macros ------------------------------------------------------------*/

/* Private variables ---------------------------------------------------------*/
static mState_t mainState;
static uint32_t idleCounter;
APP_TIMER_DEF(idleTimer);
static pendingFlashOp_t pendingFlashOp;

/* Private functions ---------------------------------------------------------*/

/**@brief Handler for shutdown preparation.
 *
 * @details During shutdown procedures, this function will be called at a 1 second interval
 *          untill the function returns true. When the function returns true, it means that the
 *          app is ready to reset to DFU mode.
 *
 * @param[in]   event   Power manager event.
 *
 * @retval  True if shutdown is allowed by this power manager handler, otherwise false.
 */
static bool app_shutdown_handler(nrf_pwr_mgmt_evt_t event)
{
    switch (event)
    {
        case NRF_PWR_MGMT_EVT_PREPARE_DFU:
        case NRF_PWR_MGMT_EVT_PREPARE_RESET:
            NRF_LOG_INFO("Power management wants to reset.");
            return true;

        case NRF_PWR_MGMT_EVT_PREPARE_WAKEUP:
        case NRF_PWR_MGMT_EVT_PREPARE_SYSOFF:
            NRF_LOG_INFO("Power management wants to enter sysoff.");
            hmi_SetLed(HMI_LT_RED, HMI_LS_OFF);
            hmi_SetLed(HMI_LT_GREEN, HMI_LS_OFF);
            hmi_SetLed(HMI_LT_BLUE, HMI_LS_OFF);
            return true;
    }

    return true;
}

//lint -esym(528, m_app_shutdown_handler)
/**@brief Register application shutdown handler with priority 0.
 */
NRF_PWR_MGMT_HANDLER_REGISTER(app_shutdown_handler, 0);

/*static void softdeviceStateObserverHandler(nrf_sdh_state_evt_t state, void * p_context)
{
    NRF_LOG_INFO("state observer %d", state);

    if (state == NRF_SDH_EVT_STATE_DISABLED)
    {
        // Softdevice was disabled before going into reset. Inform bootloader to skip CRC on next boot.
        nrf_power_gpregret2_set(BOOTLOADER_DFU_SKIP_CRC);

        //Go to system off.
        nrf_pwr_mgmt_shutdown(NRF_PWR_MGMT_SHUTDOWN_GOTO_SYSOFF);
    }
}*/

/* nrf_sdh state observer. */
/*NRF_SDH_STATE_OBSERVER(softdeviceStateObserver, 0) =
{
    .handler = softdeviceStateObserverHandler,
};*/

static void idleTimerCallback(void * pContext)
{
    (void)pContext;

    if (idleCounter == 0 || (--idleCounter != 0))
        return;

    mainState = MAINSTATE_STANDBY;
    NRF_LOG_INFO("going to standby mode");

    ret_code_t errCode;
    errCode = lm_SetExposureMode(LM_EXP_LOW_POWER);
    LOG_ERROR_CHECK("exposure mode set error %d", errCode);
    errCode = brd_SetPowerMode(BRD_PM_STANDBY);
    LOG_ERROR_CHECK("board power mode set error %d", errCode);
    errCode = app_timer_stop(idleTimer);
    LOG_ERROR_CHECK("idle timer stop error %d", errCode);
}

/**@brief Function for the main module initialization.
 *
 * @details Initializes the timer module. This creates and starts application timers.
 */
static ret_code_t mainInit(void)
{
    ret_code_t errCode, retCode = NRF_SUCCESS;

    // Initialize timer module.
    errCode = app_timer_init();
    LOG_ERROR_CHECK("timer init error %d", errCode);
    if (retCode == NRF_SUCCESS)
        retCode = errCode;

    // Initialize power management module
    errCode = nrf_pwr_mgmt_init();
    LOG_ERROR_CHECK("power management init error %d", errCode);
    if (retCode == NRF_SUCCESS)
        retCode = errCode;

    errCode = app_timer_create(&idleTimer, APP_TIMER_MODE_REPEATED, &idleTimerCallback);
    LOG_ERROR_CHECK("idle timer create error %d", errCode);
    if (retCode == NRF_SUCCESS)
        retCode = errCode;

    return retCode;
}

static void statusLedHandling(bool limiterActive)
{
    static uint32_t const processRate = APP_TIMER_TICKS(20);
    static uint32_t lastCheck;
    uint32_t timestamp;
    hmi_ledState_t ledState;

    timestamp = app_timer_cnt_get();
    if (app_timer_cnt_diff_compute(timestamp, lastCheck) < processRate)
        return;

    lastCheck = timestamp;

    // in standby and off mode deactivate leds to save energy
    /*if (mainState <= MAINSTATE_STANDBY)
    {
        hmi_SetLed(HMI_LT_RED, HMI_LS_OFF);
        hmi_SetLed(HMI_LT_GREEN, HMI_LS_OFF);
        hmi_SetLed(HMI_LT_BLUE, HMI_LS_OFF);
        return;
    }*/

    // red indicates limiter status
    //ledState = limiterActive ? HMI_LS_ON : HMI_LS_OFF;
    //hmi_SetLed(HMI_LT_RED, ledState);

    // green indicates a peripheral connection
    lm_advState_t advMode = lm_GetAdvertisingState();
    uint8_t periphCnt = lm_GetPeriphCnt();
    ledState = advMode == LM_ADV_OPEN ? HMI_LS_BLINKFAST :
               periphCnt ? HMI_LS_ON :
               advMode == LM_ADV_SLOW || advMode == LM_ADV_FAST ? HMI_LS_BLINKSLOW :
               HMI_LS_OFF;
    hmi_SetLed(HMI_LT_GREEN, ledState);

    // blue indicates scanner and central connection
    lm_scanState_t scanMode = lm_GetScanningState();
    uint8_t centralCnt = lm_GetCentralCnt();
    ledState = scanMode == LM_SCAN_SEARCH ? HMI_LS_BLINKFAST :        // blink fast if search (highest priority
               centralCnt ? HMI_LS_ON :                               // on if at least one central is connected
               scanMode == LM_SCAN_LOW_LATENCY || scanMode == LM_SCAN_LOW_POWER ? HMI_LS_BLINKSLOW :   // slow blinking if searching for known devices
               HMI_LS_OFF;                                            // or off
    hmi_SetLed(HMI_LT_BLUE, ledState);
}

/**@brief Function for handling the idle state (main loop).
 *
 * @details If there is no pending log operation, then sleep until next the next event occurs.
 */
static void main_Execute(bool limiting)
{
    statusLedHandling(limiting);
}


/** @brief function to encode the helen group configuration to bluetooth lcs congiguration
 *
 * @param[out]    pGroups the array to be filled
 * @param[in/out] pCnt    in: the size of the provides array, out: the number of elements used
 */
/*static void encodeGroupConfig(uint8_t* pGroups, uint8_t* pCnt)
{
    if (pCnt == NULL)
        return;
    if (pGroups == NULL)
    {
        *pCnt = 0;
        return;
    }

    memset(pGroups, 0, *pCnt);

    uint_fast8_t i = 0, j = 0;
    mm_modeConfig_t const* pMode;// = mm_GetModeConfig(i);
    (void)mm_GetModeConfigs(&pMode);
    while (i < MM_NUM_OF_MODES && j < *pCnt)
    {
        pGroups[j] += 1;
        if (pMode[i++].lastInGroup)
            j++;
        //pMode = mm_GetModeConfig(++i);
    }
    *pCnt = j;
}*/

/** @brief function to encode the helen mode configuration to bluetooth lcs config
 *
 * @param[in]     start    the start index to start with
 * @param[out]    pList    pointer to list, that will be filled
 * @param[in/out] pCnt     in: the size of the list, out: the number of filled elements
 */
/*static void encodeModeConfig(uint8_t start, ble_lcs_hlmt_mode_t* pList, uint8_t* pCnt)
{
    if (pCnt == NULL)   return;

    if (pList == NULL)
    {
        *pCnt = 0;
        return;
    }

    memset(pList, 0, sizeof(ble_lcs_hlmt_mode_t) * *pCnt);

    cht_5int3mode_t const* pChannels;
    uint16_t channelSize;
    brd_GetChannelConfig((void const**)&pChannels, &channelSize);
    channelSize = channelSize < 8 ? channelSize : 8;   // ignoring PMW channel so far, will fail if helena base board is available

    uint_fast8_t j = 0;
    mm_modeConfig_t const* pMode;// = mm_GetModeConfig(start);
    (void)mm_GetModeConfigs(&pMode);
    while (start < MM_NUM_OF_MODES && j < *pCnt)
    {
        pList[j].setup.spot = pMode[start].ignore ? 0 : 1;
        pList[j].setup.taillight = 0;
        pList[j].setup.brakelight = 0;
        if (j < channelSize && !pMode[start++].ignore)
        {
            pList[j].intensity = CHT_53_TO_PERCENT(pChannels[j].intensity);
            if (pChannels[j].intensity == 0)
                pList[j].setup.spot = 0;
            pList[j].setup.pitchCompensation = pChannels[j].mode == 1 ? 1 : 0;
        }                                                       //  ^ just temporary for LCS
        else
        {
            pList[j].intensity = 0;
            pList[j].setup.spot = 0;
        }
        //pMode = mm_GetModeConfig(++start);
        j++;
    }
    *pCnt = j;
}*/

static void flashOpResultHandler(ret_code_t errCode)
{
    if (pendingFlashOp.pendingResponses == 0)
        return; // not expecting anything

    // preserve the first error code
    if (pendingFlashOp.firstErrorCode == NRF_SUCCESS)
        pendingFlashOp.firstErrorCode = errCode;

    if (--pendingFlashOp.pendingResponses == 0)
    {
        switch (pendingFlashOp.source)
        {
        /*case FLOPSCR_LCS:
        {
            ret_code_t errCode;
            ble_lcs_ctrlpt_rsp_t rsp = {0};
            rsp.opcode = pendingFlashOp.lcs.event +
                         BLE_LCS_CTRLPT_OP_CODE_REQ_MODE_CNT - BLE_LCS_CTRLPT_EVT_REQ_MODE_CNT;
            if (pendingFlashOp.firstErrorCode == NRF_SUCCESS)
                rsp.status = BLE_LCS_CTRLPT_RSP_CODE_SUCCESS;
            else if (pendingFlashOp.firstErrorCode == NRF_ERROR_INVALID_PARAM)
                rsp.status = BLE_LCS_CTRLPT_RSP_CODE_INVALID;
            else
                rsp.status = BLE_LCS_CTRLPT_RSP_CODE_FAILED;
            errCode = ble_lcs_ctrlpt_mode_resp(pendingFlashOp.lcs.pLcsCtrlpt, pendingFlashOp.lcs.connHandle, &rsp);
            LOG_ERROR_CHECK("error %d sending control point response", errCode);
        }   break;*/

        case FLOPSCR_HMI:
            if (pendingFlashOp.hmiResponse != NULL)
                pendingFlashOp.hmiResponse(pendingFlashOp.firstErrorCode);
            break;

        default:
            break;
        }

        memset(&pendingFlashOp, 0, sizeof(pendingFlashOp));
    }
}

/*static void lcsCpErrorHandler(uint32_t errCode)
{
    NRF_LOG_ERROR("lcs cp error: %d", errCode);
}*/

static bool isBlockZero(void const* pBlock, unsigned int size)
{
    unsigned char* pMem = (unsigned char*)pBlock;
    for (unsigned int i = 0; i < size; i++)
    {
        if(pMem[i] != 0)
            return false;
    }
    return true;
}

/*static void lcsCpEventHandler(ble_lcs_ctrlpt_t * pLcsCtrlpt, ble_lcs_ctrlpt_evt_t * pEvt)
{
    ret_code_t errCode;
    ble_lcs_ctrlpt_rsp_t rsp = {0};
    rsp.opcode = pEvt->evt_type + BLE_LCS_CTRLPT_OP_CODE_REQ_MODE_CNT - BLE_LCS_CTRLPT_EVT_REQ_MODE_CNT;
    rsp.status = BLE_LCS_CTRLPT_RSP_CODE_SUCCESS;

    union
    {
        uint8_t groupCfg[MM_NUM_OF_MODES];
        ble_lcs_hlmt_mode_t modeList[MM_NUM_OF_MODES];
    } data;

    switch (pEvt->evt_type)
    {
    case BLE_LCS_CTRLPT_EVT_REQ_MODE_CNT:
        NRF_LOG_DEBUG("number of modes requested");
        rsp.params.mode_cnt = MM_NUM_OF_MODES;
        break;
    case BLE_LCS_CTRLPT_EVT_SET_MODE:
    {
        NRF_LOG_DEBUG("request to set mode to %d", pEvt->p_params->set_mode);
        hmi_evtParams_t modeReq;
        modeReq.mode.connHandle = pEvt->conn_handle;
        modeReq.mode.modeNumber = pEvt->p_params->set_mode;
        if (hmi_RequestEvent(HMI_EVT_MODENUMBER, &modeReq) != NRF_SUCCESS)
            rsp.status = BLE_LCS_CTRLPT_RSP_CODE_FAILED;
    }   break;
    case BLE_LCS_CTRLPT_EVT_REQ_GRP_CNFG:
    {
        NRF_LOG_DEBUG("group organization requested");
        uint8_t cnt = ARRAY_SIZE(data.groupCfg);
        encodeGroupConfig(data.groupCfg, &cnt);
        rsp.params.group_config.num_of_groups = cnt;
        rsp.params.group_config.p_list_of_modes_per_group = data.groupCfg;
    }   break;

    case BLE_LCS_CTRLPT_EVT_CNFG_GROUP:
        NRF_LOG_DEBUG("new group organization received");

        if (pendingFlashOp.pendingResponses)
        {
            rsp.status = BLE_LCS_CTRLPT_RSP_CODE_NOT_SUPPORTED;
            break;
        }

        pendingFlashOp.pendingResponses = 1;
        pendingFlashOp.source = FLOPSCR_LCS;
        pendingFlashOp.lcs.event = pEvt->evt_type;
        pendingFlashOp.lcs.pLcsCtrlpt = pLcsCtrlpt;
        pendingFlashOp.lcs.connHandle = pEvt->conn_handle;
        errCode = mm_UpdateGroupConfig(&pEvt->p_params->group_config, flashOpResultHandler);
        if (errCode != NRF_SUCCESS)     // report manually if request fails
            flashOpResultHandler(errCode);
        return;

    case BLE_LCS_CTRLPT_EVT_REQ_MODE_CNFG:
    {
        NRF_LOG_DEBUG("mode organization requested");
        uint8_t cnt = ARRAY_SIZE(data.modeList);
        encodeModeConfig(pEvt->p_params->mode_list_start, data.modeList, &cnt);
        rsp.params.mode_config_list.num_of_entries = cnt;
        rsp.params.mode_config_list.p_list_hlmt = data.modeList;
    }   break;

    case BLE_LCS_CTRLPT_EVT_CNFG_MODE:
        NRF_LOG_DEBUG("new mode organization received");

        if (pendingFlashOp.pendingResponses)
        {
            rsp.status = BLE_LCS_CTRLPT_RSP_CODE_NOT_SUPPORTED;
            break;
        }

        pendingFlashOp.pendingResponses = 2;
        pendingFlashOp.source = FLOPSCR_LCS;
        pendingFlashOp.lcs.event = pEvt->evt_type;
        pendingFlashOp.lcs.pLcsCtrlpt = pLcsCtrlpt;
        pendingFlashOp.lcs.connHandle = pEvt->conn_handle;

        errCode = mm_UpdateModeConfig(&pEvt->p_params->mode_config, flashOpResultHandler);
        if (errCode != NRF_SUCCESS)     // report manually if request fails
            flashOpResultHandler(errCode);

        errCode = brd_UpdateChannelConfig(&pEvt->p_params->mode_config, flashOpResultHandler);
        if (errCode != NRF_SUCCESS)     // report manually if request fails
            flashOpResultHandler(errCode);

        return;

    case BLE_LCS_CTRLPT_EVT_REQ_LED_CNFG:
        NRF_LOG_DEBUG("led configuration requested");
        rsp.params.led_config.cnt_spot = 2; // hardcoded for now
        break;

    case BLE_LCS_CTRLPT_EVT_REQ_PREF_MODE:
        NRF_LOG_DEBUG("preferred mode requested");
        rsp.params.pref_mode = mm_GetPrefMode();
        break;

    case BLE_LCS_CTRLPT_EVT_SET_PREF_MODE:
        NRF_LOG_DEBUG("new preferred mode (%d) received", pEvt->p_params->pref_mode);

        if (pendingFlashOp.pendingResponses)
        {
            rsp.status = BLE_LCS_CTRLPT_RSP_CODE_NOT_SUPPORTED;
            break;
        }

        pendingFlashOp.pendingResponses = 1;
        pendingFlashOp.source = FLOPSCR_LCS;
        pendingFlashOp.lcs.event = pEvt->evt_type;
        pendingFlashOp.lcs.pLcsCtrlpt = pLcsCtrlpt;
        pendingFlashOp.lcs.connHandle = pEvt->conn_handle;
        errCode = mm_SetPrefMode(pEvt->p_params->pref_mode, flashOpResultHandler);
        if (errCode != NRF_SUCCESS)     // report manually if request fails
            flashOpResultHandler(errCode);
        return;

    case BLE_LCS_CTRLPT_EVT_REQ_TEMP_MODE:
        NRF_LOG_DEBUG("temporary mode requested");
        rsp.params.temp_mode = mm_GetTempMode();
        break;

    case BLE_LCS_CTRLPT_EVT_SET_TEMP_MODE:
        NRF_LOG_DEBUG("new temporary mode (%d) received", pEvt->p_params->pref_mode);

        if (pendingFlashOp.pendingResponses)
        {
            rsp.status = BLE_LCS_CTRLPT_RSP_CODE_NOT_SUPPORTED;
            break;
        }

        pendingFlashOp.pendingResponses = 1;
        pendingFlashOp.source = FLOPSCR_LCS;
        pendingFlashOp.lcs.event = pEvt->evt_type;
        pendingFlashOp.lcs.pLcsCtrlpt = pLcsCtrlpt;
        pendingFlashOp.lcs.connHandle = pEvt->conn_handle;
        errCode = mm_SetTempMode(pEvt->p_params->temp_mode, flashOpResultHandler);
        if (errCode != NRF_SUCCESS)     // report manually if request fails
            flashOpResultHandler(errCode);
        return;

    case BLE_LCS_CTRLPT_EVT_CHK_LED_CNFG:
    case BLE_LCS_CTRLPT_EVT_REQ_SENS_OFF:
    case BLE_LCS_CTRLPT_EVT_CALIB_SENS_OFF:
    case BLE_LCS_CTRLPT_EVT_REQ_LIMITS:
    case BLE_LCS_CTRLPT_EVT_SET_LIMITS:
    default:
        rsp.status = BLE_LCS_CTRLPT_RSP_CODE_NOT_SUPPORTED;
        break;
    }

    errCode = ble_lcs_ctrlpt_mode_resp(pLcsCtrlpt, pEvt->conn_handle, &rsp);
    APP_ERROR_CHECK(errCode);
}*/
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
int main(void)
{
    //dbg_StartCycleCnt();
    //dbg_ResetCycleCnt();

    ret_code_t errCode, criticalError = NRF_SUCCESS;
    brd_info_t const* pBrdInfos;
    uint8_t initMode;

    //nrf_power_system_off();

    errCode = dbg_Init();
    APP_ERROR_CHECK(errCode);

    errCode = mainInit();
    APP_ERROR_CHECK(errCode);

    // First of all initialize the mode management, so that the modes are
    // already for the board initialization
    errCode = mm_Init(modeChanged, &initMode);
    APP_ERROR_CHECK(errCode);

    errCode = brd_Init(&pBrdInfos);
    LOG_ERROR_CHECK("board init error %d", errCode);
    if (criticalError == NRF_SUCCESS)
        criticalError = errCode;

    hmi_init_t hmiInit = {.eventHandler = hmiEventHandler};
    errCode = hmi_Init(&hmiInit);
    APP_ERROR_CHECK(errCode);

    errCode = bluetoothInit(pBrdInfos);
    APP_ERROR_CHECK(errCode);

    /*while(1)
    {
        __WFE();
    }*/

    errCode = comInit(&pBrdInfos->pFeatures->comSupported);
    APP_ERROR_CHECK(errCode);

    if (criticalError)
        hmi_SetLed(HMI_LT_RED, HMI_LS_BLINKFAST);
    while (criticalError)
    {
        wdg_Feed();
    }

    mainState = MAINSTATE_STANDBY;
    idleCounter = 0;

    errCode = brd_SetPowerMode(BRD_PM_STANDBY);
    APP_ERROR_CHECK(errCode);

    errCode = lm_SetExposureMode(LM_EXP_LOW_POWER);
    APP_ERROR_CHECK(errCode);

    if (initMode == MM_MODE_OFF)
        initMode = mm_GetOffMode();
    errCode = brd_SetLightMode(initMode);
    APP_ERROR_CHECK(errCode);

    NRF_LOG_INFO("entering main loop");

    // Enter main loop.
    for (;;)
    {
        bool limiting;

        limiting = brd_Execute();                       /// TODO: changed, test again! 518 - 52000 cycles

        hmi_Execute();                                  // ~7 cycles

        main_Execute(limiting);                         // ~72-1300 cycles

        if (dbg_Execute() == false)
        {
            nrf_pwr_mgmt_run();
        }
    }
}

/* Public functions ----------------------------------------------------------*/
ret_code_t main_ResetIdleTimer()
{
    ret_code_t errCode = NRF_SUCCESS;

    if (mainState <= MAINSTATE_STANDBY)
    {
        mainState = MAINSTATE_IDLE;
        errCode = app_timer_start(idleTimer, IDLE_PERIOD, NULL);
        LOG_ERROR_CHECK("starting idle timer error %d", errCode);
        NRF_LOG_INFO("going to idle mode");
        errCode = lm_SetExposureMode(LM_EXP_LOW_LATENCY);
        LOG_ERROR_CHECK("exposure mode set error %d", errCode);
        errCode = brd_SetPowerMode(BRD_PM_IDLE);
        LOG_ERROR_CHECK("board power mode set error %d", errCode);
    }

    idleCounter = IDLE_TIMEOUT / IDLE_PERIOD;

    return errCode;
}

/**END OF FILE*****************************************************************/

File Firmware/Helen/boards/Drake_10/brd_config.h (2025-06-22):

/**
 * Copyright (c) 2017 - 2021, Nordic Semiconductor ASA
 *
 * All rights reserved.
 *
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
 * 3. Neither the name of Nordic Semiconductor ASA nor the names of its
 *    contributors may be used to endorse or promote products derived from this
 *    software without specific prior written permission.
 *
 * 4. This software, with or without modification, must only be used with a
 *    Nordic Semiconductor ASA integrated circuit.
 *
 * 5. Any software provided in binary form under this license must not be reverse
 *    engineered, decompiled, modified and/or disassembled.
 *
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
 */



#ifndef BRD_CONFIG_H
#define BRD_CONFIG_H
// <<< Use Configuration Wizard in Context Menu >>>\n

// <o> NRF_SDH_BLE_GATTS_ATTR_TAB_SIZE - Attribute Table size in bytes. The size must be a multiple of 4.
#ifndef NRF_SDH_BLE_GATTS_ATTR_TAB_SIZE
#define NRF_SDH_BLE_GATTS_ATTR_TAB_SIZE 1536
#endif

//==========================================================

// <h> nRF_BLE_Services

//==========================================================

// <e> BLE_BAS_ENABLED - ble_bas - Battery Service
//==========================================================
#ifndef BLE_BAS_ENABLED
#define BLE_BAS_ENABLED 1
#endif
// <e> BLE_BAS_CONFIG_LOG_ENABLED - Enables logging in the module.
//==========================================================
#ifndef BLE_BAS_CONFIG_LOG_ENABLED
#define BLE_BAS_CONFIG_LOG_ENABLED 0
#endif
// <o> BLE_BAS_CONFIG_LOG_LEVEL  - Default Severity level

// <0=> Off
// <1=> Error
// <2=> Warning
// <3=> Info
// <4=> Debug

#ifndef BLE_BAS_CONFIG_LOG_LEVEL
#define BLE_BAS_CONFIG_LOG_LEVEL 3
#endif

// <o> BLE_BAS_CONFIG_INFO_COLOR  - ANSI escape code prefix.

// <0=> Default
// <1=> Black
// <2=> Red
// <3=> Green
// <4=> Yellow
// <5=> Blue
// <6=> Magenta
// <7=> Cyan
// <8=> White

#ifndef BLE_BAS_CONFIG_INFO_COLOR
#define BLE_BAS_CONFIG_INFO_COLOR 0
#endif

// <o> BLE_BAS_CONFIG_DEBUG_COLOR  - ANSI escape code prefix.

// <0=> Default
// <1=> Black
// <2=> Red
// <3=> Green
// <4=> Yellow
// <5=> Blue
// <6=> Magenta
// <7=> Cyan
// <8=> White

#ifndef BLE_BAS_CONFIG_DEBUG_COLOR
#define BLE_BAS_CONFIG_DEBUG_COLOR 0
#endif

// </e>

// </e>

// </h>

// <h> nRF_Drivers

//==========================================================
// <e> NRFX_CLOCK_ENABLED - nrfx_clock - CLOCK peripheral driver
//==========================================================
#ifndef NRFX_CLOCK_ENABLED
#define NRFX_CLOCK_ENABLED 0
#endif
// <o> NRFX_CLOCK_CONFIG_LF_SRC  - LF Clock Source

// <0=> RC
// <1=> XTAL
// <2=> Synth
// <131073=> External Low Swing
// <196609=> External Full Swing

#ifndef NRFX_CLOCK_CONFIG_LF_SRC
#define NRFX_CLOCK_CONFIG_LF_SRC 1
#endif

// <o> NRFX_CLOCK_CONFIG_IRQ_PRIORITY  - Interrupt priority

// <0=> 0 (highest)
// <1=> 1
// <2=> 2
// <3=> 3
// <4=> 4
// <5=> 5
// <6=> 6
// <7=> 7

#ifndef NRFX_CLOCK_CONFIG_IRQ_PRIORITY
#define NRFX_CLOCK_CONFIG_IRQ_PRIORITY 6
#endif

// <e> NRFX_CLOCK_CONFIG_LOG_ENABLED - Enables logging in the module.
//==========================================================
#ifndef NRFX_CLOCK_CONFIG_LOG_ENABLED
#define NRFX_CLOCK_CONFIG_LOG_ENABLED 0
#endif
// <o> NRFX_CLOCK_CONFIG_LOG_LEVEL  - Default Severity level

// <0=> Off
// <1=> Error
// <2=> Warning
// <3=> Info
// <4=> Debug

#ifndef NRFX_CLOCK_CONFIG_LOG_LEVEL
#define NRFX_CLOCK_CONFIG_LOG_LEVEL 3
#endif

// <o> NRFX_CLOCK_CONFIG_INFO_COLOR  - ANSI escape code prefix.

// <0=> Default
// <1=> Black
// <2=> Red
// <3=> Green
// <4=> Yellow
// <5=> Blue
// <6=> Magenta
// <7=> Cyan
// <8=> White

#ifndef NRFX_CLOCK_CONFIG_INFO_COLOR
#define NRFX_CLOCK_CONFIG_INFO_COLOR 0
#endif

// <o> NRFX_CLOCK_CONFIG_DEBUG_COLOR  - ANSI escape code prefix.

// <0=> Default
// <1=> Black
// <2=> Red
// <3=> Green
// <4=> Yellow
// <5=> Blue
// <6=> Magenta
// <7=> Cyan
// <8=> White

#ifndef NRFX_CLOCK_CONFIG_DEBUG_COLOR
#define NRFX_CLOCK_CONFIG_DEBUG_COLOR 0
#endif

// </e>

// </e>

// <e> NRFX_COMP_ENABLED - nrfx_comp - COMP peripheral driver
//==========================================================
#ifndef NRFX_COMP_ENABLED
#define NRFX_COMP_ENABLED 1
#endif
// <o> NRFX_COMP_CONFIG_REF  - Reference voltage

// <0=> Internal 1.2V
// <1=> Internal 1.8V
// <2=> Internal 2.4V
// <4=> VDD
// <7=> ARef

#ifndef NRFX_COMP_CONFIG_REF
#define NRFX_COMP_CONFIG_REF 4
#endif

// <o> NRFX_COMP_CONFIG_MAIN_MODE  - Main mode

// <0=> Single ended
// <1=> Differential

#ifndef NRFX_COMP_CONFIG_MAIN_MODE
#define NRFX_COMP_CONFIG_MAIN_MODE 0
#endif

// <o> NRFX_COMP_CONFIG_SPEED_MODE  - Speed mode

// <0=> Low power
// <1=> Normal
// <2=> High speed

#ifndef NRFX_COMP_CONFIG_SPEED_MODE
#define NRFX_COMP_CONFIG_SPEED_MODE 2
#endif

// <o> NRFX_COMP_CONFIG_HYST  - Hystheresis

// <0=> No
// <1=> 50mV

#ifndef NRFX_COMP_CONFIG_HYST
#define NRFX_COMP_CONFIG_HYST 0
#endif

// <o> NRFX_COMP_CONFIG_ISOURCE  - Current Source

// <0=> Off
// <1=> 2.5 uA
// <2=> 5 uA
// <3=> 10 uA
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

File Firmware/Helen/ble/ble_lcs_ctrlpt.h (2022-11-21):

/**
  ******************************************************************************
  * @file    ble_lcs_ctrlpt.h
  * @author  Thomas Reisnecker
  * @version V1.0
  * @date    16/11/08
  * @brief   Light Control Service control point implementation
  *
  * @details This module implements the Light Control Service control behavior.
  *          It is used by the Control Point Service module for control point
  *          mechanisms like configuring and setting light modes and grouping.
  ******************************************************************************
  */

/* Define to prevent recursive inclusion -------------------------------------*/
#ifndef BLE_LCS_CTRLPT_H_INCLUDED
#define BLE_LCS_CTRLPT_H_INCLUDED

/* Includes ------------------------------------------------------------------*/
#include "ble_lcs.h"

/* Exported defines ----------------------------------------------------------*/
#define BLE_LCS_CTRLPT_MAX_LEN                  19
#define BLE_LCS_CTRLPT_MIN_LEN                  1

#define BLE_LCS_CTRLPT_MIN_RESPONSE_SIZE        3
#define BLE_LCS_CTRLPT_MAX_RESPONSE_SIZE        19

#define BLE_LCS_CTRLPT_OPCODE_POS               0
#define BLE_LCS_CTRLPT_PARAMETER_POS            1
#define BLE_LCS_CTRLPT_REQUEST_OPCODE_POS       1
#define BLE_LCS_CTRLPT_RESPONSE_CODE_POS        2
#define BLE_LCS_CTRLPT_RESPONSE_PARAMETER_POS   3

#define BLE_LCS_CTRLPT_MAX_NUM_OF_MODES         8

/* Exported types ------------------------------------------------------------*/
/**@brief Light Control Service Control Point event types */
typedef enum
{
    BLE_LCS_CTRLPT_EVT_REQ_MODE_CNT,    /**< Operator to request mode count */
    BLE_LCS_CTRLPT_EVT_SET_MODE,        /**< Operator to set a specific mode */
    BLE_LCS_CTRLPT_EVT_REQ_GRP_CNFG,    /**< Operator to request number of mode groups */
    BLE_LCS_CTRLPT_EVT_CNFG_GROUP,      /**< Operator to configure grouping */
    BLE_LCS_CTRLPT_EVT_REQ_MODE_CNFG,   /**< Operator to request a list of mode configurations */
    BLE_LCS_CTRLPT_EVT_CNFG_MODE,       /**< Operator to configure a specific mode */
    BLE_LCS_CTRLPT_EVT_REQ_LED_CNFG,    /**< Operator to request current led configuration */
    BLE_LCS_CTRLPT_EVT_CHK_LED_CNFG,    /**< Operator to start the check procedure for led configuration */
    BLE_LCS_CTRLPT_EVT_REQ_SENS_OFF,    /**< Operator to request the current sensor offset values */
    BLE_LCS_CTRLPT_EVT_CALIB_SENS_OFF,  /**< Operator to start the sensor offset calibration */
    BLE_LCS_CTRLPT_EVT_REQ_LIMITS,      /**< Operator to request the current current limits */
    BLE_LCS_CTRLPT_EVT_SET_LIMITS,      /**< Operator to set the current limits  */
    BLE_LCS_CTRLPT_EVT_REQ_PREF_MODE,   /**< Operator to request the current preferred mode */
    BLE_LCS_CTRLPT_EVT_SET_PREF_MODE,   /**< Operator to set the preferred mode */
    BLE_LCS_CTRLPT_EVT_REQ_TEMP_MODE,   /**< Operator to request the current temporary mode */
    BLE_LCS_CTRLPT_EVT_SET_TEMP_MODE,   /**< Operator to set the temporary mode */
} ble_lcs_ctrlpt_evt_type_t;

/**@brief Light Control Control Point mode configuration structure */
typedef struct
{
    uint8_t                 mode_number_start;
    uint8_t                 mode_entries;
    union
    {
        ble_lcs_hlmt_mode_t config_hlmt[BLE_LCS_CTRLPT_MAX_NUM_OF_MODES];
        ble_lcs_bk_mode_t   config_bk[BLE_LCS_CTRLPT_MAX_NUM_OF_MODES];
        //ble_lcs_tl_mode_t   config_tl[BLE_LCS_CTRLPT_MAX_NUM_OF_MODES];
    };
} ble_lcs_ctrlpt_mode_cnfg_t;

/**@brief Light Control Control Point group configuration structure */
typedef struct
{
    uint8_t         number_of_groups;
    uint8_t const * p_list_of_modes_per_group;    /** NULL, if no individual group configuration available */
} ble_lcs_ctrlpt_group_cnfg_t;

/**@brief Light Control Control Point set current limits structure */
typedef union
{
    struct
    {
        int8_t  flood;
        int8_t  spot;
    };
    struct
    {
        int8_t  main_beam;
        int8_t  high_beam;
    };
} ble_lcs_ctrlpt_set_limits_t;

/**@brief Light Control Service Control Point write values */
typedef union
{
    uint8_t                     mode_list_start;
    uint8_t                     set_mode;
    ble_lcs_ctrlpt_mode_cnfg_t  mode_config;
    ble_lcs_ctrlpt_group_cnfg_t group_config;
    ble_lcs_ctrlpt_set_limits_t current_limits;
    uint8_t                     pref_mode;
    uint8_t                     temp_mode;
} ble_lcs_ctrlpt_write_val_t;

/**@brief Light Control Control Point response parameter */
typedef enum
{
    BLE_LCS_CTRLPT_RSP_CODE_SUCCESS       = 1,
    BLE_LCS_CTRLPT_RSP_CODE_NOT_SUPPORTED = 2,
    BLE_LCS_CTRLPT_RSP_CODE_INVALID       = 3,
    BLE_LCS_CTRLPT_RSP_CODE_FAILED        = 4
} ble_lcs_ctrlpt_rsp_code_t;

/**@brief Light Control Control Point response indication structure */
typedef struct
{
    ble_lcs_ctrlpt_rsp_code_t rsp_code;
    uint8_t                   len;
    uint8_t                   encoded_rsp[BLE_LCS_CTRLPT_MAX_LEN];
} ble_lcs_ctrlpt_rsp_ind_t;

/**@brief Light Control Control Point procedure status */
typedef enum
{
    BLE_LCS_CTRLPT_PROC_STATUS_FREE             = 0,
    BLE_LCS_CTRLPT_PROC_IN_PROGRESS             = 1,
    BLE_LCS_CTRLPT_RSP_CODE_IND_PENDING         = 2,
    BLE_LCS_CTRLPT_RSP_CODE_IND_CONFIRM_PENDING = 3
} ble_lcs_ctrlpt_proc_status_t;

typedef struct
{
    uint16_t                     conn_handle;       /**< Handle of the current connection (as provided by the BLE stack) */
    ble_lcs_ctrlpt_proc_status_t procedure_status;  /**< status of possible procedure */
    ble_lcs_ctrlpt_rsp_ind_t     response;          /**< pending response data */
} ble_lcs_ctrlpt_client_spec_t;
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

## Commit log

2022-11-27 documentation update, adaptation to hardware changes
    [KD2_10.kicad_pcb, KD2_10.sch]
2024-06-20 minor bugfixes
    [6XEG.kicad_pcb, 6XEG.sch]
